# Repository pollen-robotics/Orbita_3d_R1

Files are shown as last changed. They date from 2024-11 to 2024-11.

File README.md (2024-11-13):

# Orbita_3d_R1
All you need to make your own Orbita_3d Joint!

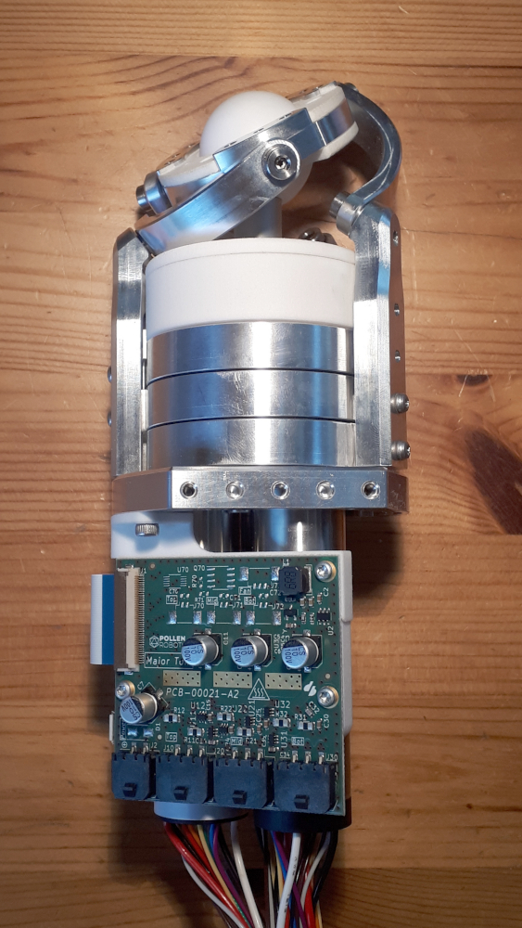
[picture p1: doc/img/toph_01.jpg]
3d view - Major_Tom


## Basically
Please find:
 - Electronic boards that controls (elec_Houston), drives (elec_Major_Tom) and measures (elec_Pacman) the Orbita 3d Joint over 12V-supplied Dynamixel bus.
 - Firmware gather communication (Dynamixel library) and motor control (SimpleFOC library)
 - Cables

## Licences
 - Firmware is under Apache-2.0 licence
 - Electronic/Cables is under CC-BY-SA-NC Licence

## Patents
https://patents.google.com/patent/FR3141363A1

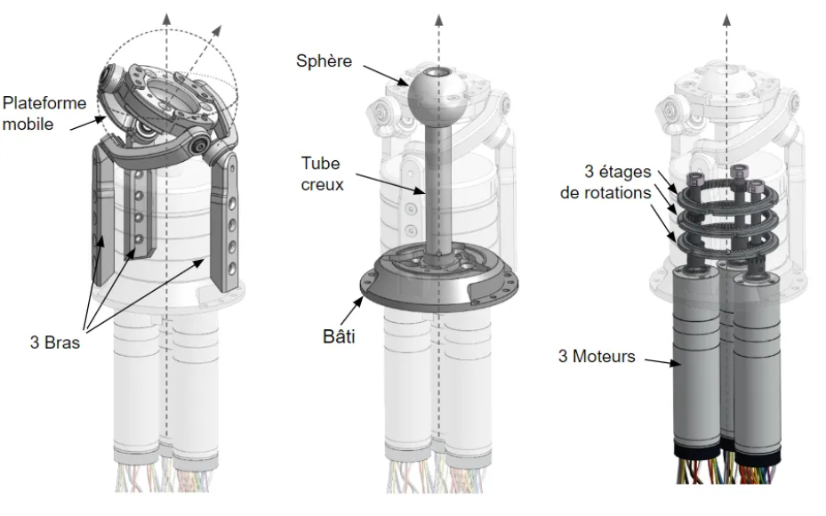
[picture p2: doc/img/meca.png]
3d view - Mecanique - FR


## Contact
contact@pollen-robotics.com

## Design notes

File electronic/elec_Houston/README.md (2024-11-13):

# Houston Electronic Board

Houston board is basically a STM32G4 microcontroller that focuses on driving 3 BLDC motors. It gets 3 Hall effects or encoders on motors and absolute positions behind reduction through SPI encoders.

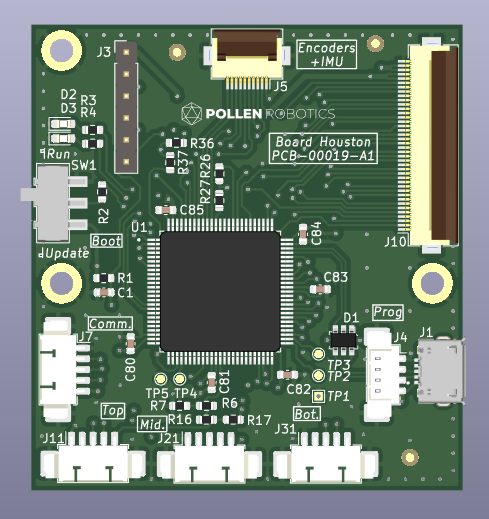
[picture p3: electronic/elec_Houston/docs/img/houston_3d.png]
houston board 3d image


## Basically
 - 50 x 54 mm
 - Powered in 3V3 through the large flat flexible connector J10
 - 5V should also be provided since it supplies encoders J11/21/31
 - Designed with KiCAD 6.0

## ST configuration

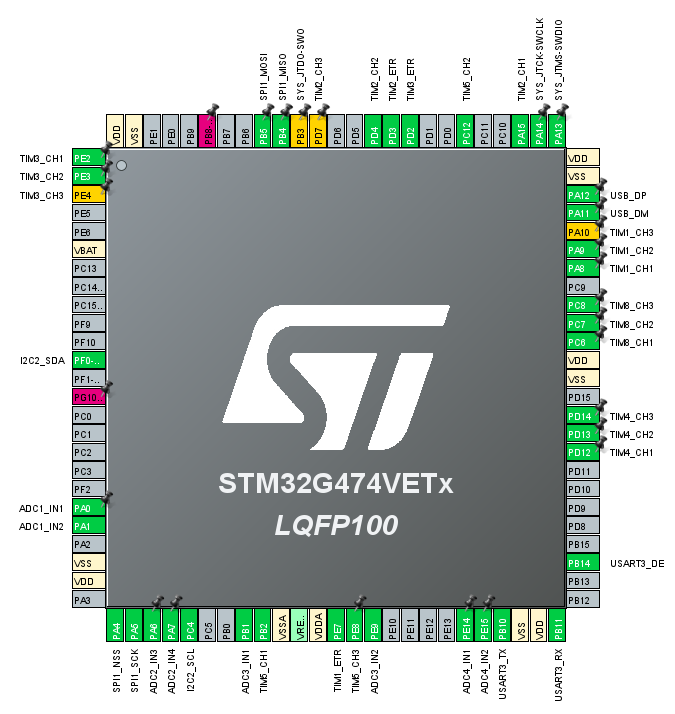
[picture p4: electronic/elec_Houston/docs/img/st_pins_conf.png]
houston board 3d image


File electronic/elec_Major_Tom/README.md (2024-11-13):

# Major Tom Electronic Board

Major Tom is a power board driving 3 BLDC motors. It also add 3 temperature measurements and a fan control.

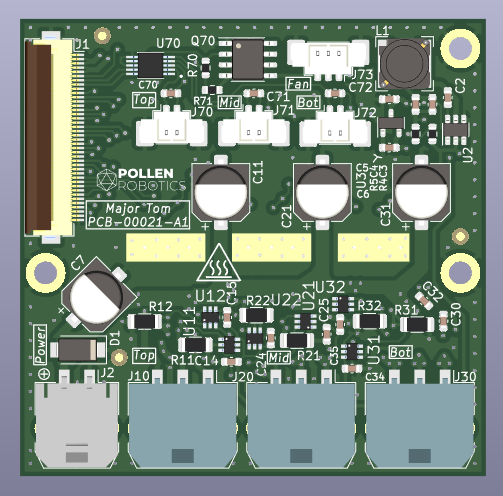
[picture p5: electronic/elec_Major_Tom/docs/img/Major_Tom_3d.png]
Major Tom board 3d image


## Basically
 - 55 x 54 mm
 - Powered in 12V or in 24V.
 - Drive 3 BLDC motors with DRV8313 (2,5 A peak)
 - Designed with KiCAD 6.

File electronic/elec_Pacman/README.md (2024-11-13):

# Pacman Electronic Board

Pacman board gathers 3 absolute encoders with an IMU. It is set at the top of the Orbita system and sends angular positions of the 3 axis + IMU data. It is connected to the Houston board through a FFC.

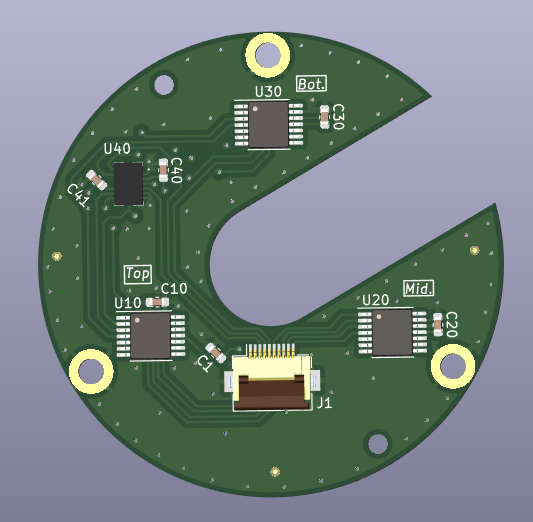
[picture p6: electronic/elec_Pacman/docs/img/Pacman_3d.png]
Pacman board 3d image


## Basically
 - 49 mm diameter with a 13 mm slot
 - Powered in 3V3
 - Common SPI, differents CS pins.

## Notas
 - all components are on the bottom side since the encoders are facing down the motors.

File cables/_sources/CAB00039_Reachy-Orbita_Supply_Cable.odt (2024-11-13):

CAB-00039 – Supply Cable – Orbita

Ver. | Date | Pub | Chk | Description
A1 | 12/01/2023 | EB | AC | Initial drawing.
B1 | 14/02/2023 | EB | AC | Turned into a Y cable to supply Reachy’s antennas.

1. Purpose

This cable supplies Orbita Motors Drivers (ASE00038 Major Tom) from Reachy’s Power Supply Board. The small part (Y cable) supply Reachy’s head through Orbita. This cable is made for Reachy 1.2.

2. Bill of Material

Item | Description | L (mm) | Qtty | Ref. Farnell / RS
Wire | 0,3 mm² | 200 | 2
Hirose DF11 Fem. Housing 8 ways | DF11-8DS-2C | | 1 | 1688304 /
MicroFit Fem. Housing 2 ways | 43645-0200 | | 1 | 3076015 /
MicroFit Male Housing 2 ways | 43640-0201 | | 1 | 3076118 /
Contacts for DF11 | DF11-2428SC | | 2 | 1688393 /
Contacts for MicroFit | 43031-0001 | | 2 | 1653819 /
Contacts for MicroFit | 46235-0001 | | 2 | 2284551 /
Prolongateur | 22 AWG – 16 AWG | | 4 | 587321 /

3. Assembly

Molex Microfit Contacts are crimped with Molex 64016-0201 Tool.

Hirose DF11 Contacts are crimped with Hirose HT801/DF11-2428S(A) Tool

4. Drawing

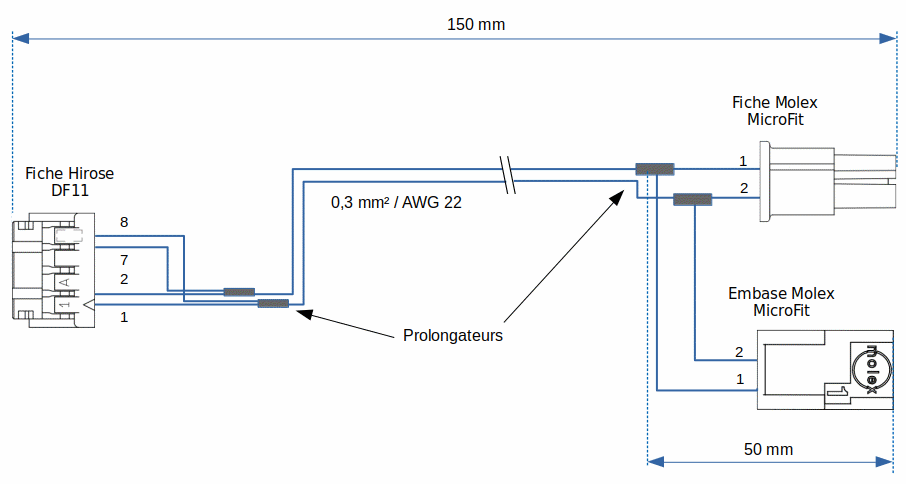
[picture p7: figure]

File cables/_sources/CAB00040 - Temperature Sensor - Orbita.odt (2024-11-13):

CAB-00040 Temperature Sensor - Orbita

Ver. | Date | Pub | Chk | Description
A1 | 13/01/2023 | EB | AC | Initial drawing.

1. Purpose

This temperature sensor is actually a bipolar transistor, its base on the linear relationship between base-emitter voltage and temperature changes. Temperatures are read by the MAX31730 on Major Tom Board.

2. Bill of Materials

Item | Description | L (mm) | Qtté | Ref. Farnell / RS
Wire | 0,15 mm² | ?? | 2
Molex PicoBlade Fem. Housing 2 ways | 51021-0200 | | 1 | /
Contacts for PicoBlade | 50079-8000 | | 2 | /
2N3904 | Transistor TO-92 | | 1 | 1574370 /
Gaine thermo | | 10 | 2

3. Assembly

Molex PicoBlade Contacts are crimped with Tool Molex 63811-0000.

4. Drawing

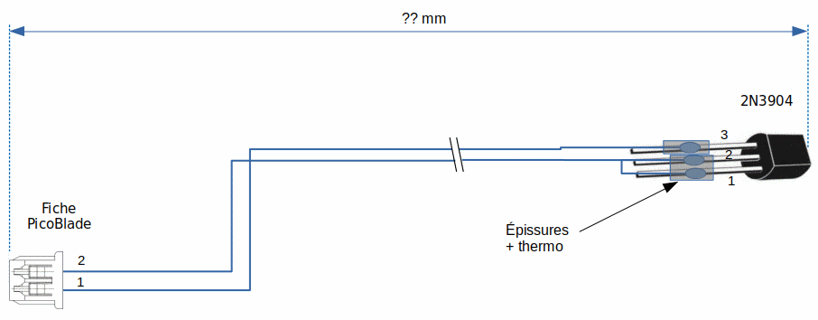
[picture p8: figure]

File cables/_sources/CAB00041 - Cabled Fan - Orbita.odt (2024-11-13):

CAB-00041 – Cabled Fan - Orbita

Ver. | Date | Pub | Chk | Description
A1 | 16/01/2023 | EB | AC | Initial drawing.

1. Purpose

This temperature sensor is actually a bipolar transistor, its base on the linear relationship between base-emitter voltage and temperature changes. Temperatures are read by the MAX31730 on Major Tom Board.

2. Bill of Materials

Item | Description | L (mm) | Qtté | Ref. Farnell / RS
Fan - 12V | RS Pro 668-8808 | | 1 | / 668-8808
Molex PicoBlade Fem. Housing 3 ways | 51021-0300 | | 1 | /
Contacts for PicoBlade | 50079-8000 | | 2 | /

3. Assembly

Molex PicoBlade Contacts are crimped with Tool Molex 63811-0000.

4. Drawing

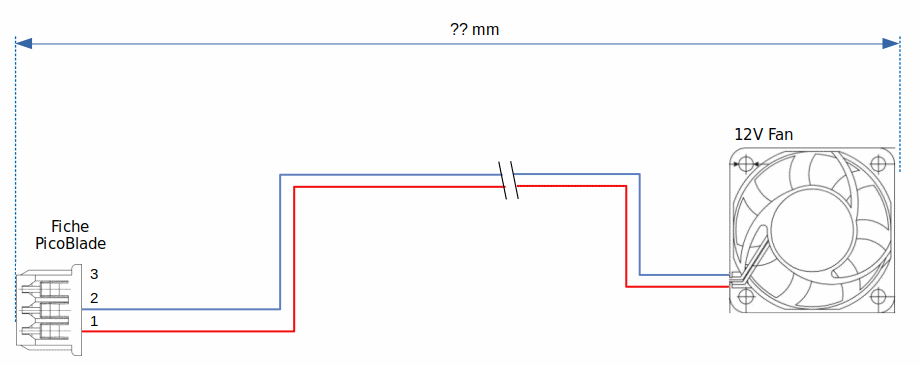
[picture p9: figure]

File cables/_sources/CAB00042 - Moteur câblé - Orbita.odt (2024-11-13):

CAB-00042 – Wired Motor – Orbita

Ver. | Date | Pub | Chk | Description
A1 | 24/01/2023 | EB | AC | Initial drawing.
B1 | 27/03/2023 | EB | AC | Now using Hall sensors

1. Description

24V BLDC Motor (+Reduction + Encoder) wired for Orbita.

2. Bill of Material

Item | Description | L (mm) | Qtté | Ref. Farnell / RS
BLDC Motor 24V + Reductor + Encoder | ECXTQ22M+GPX22R1C+ENX22 | | 1 | Provided par Pollen
Molex PicoBlade Fem. Housing 5 ways | 51021-0500 | | 1 | /
Contacts for PicoBlade | 50079-8000 | | 5 | /
Molex MicroFit Fem. Housing 3 ways | 43645-0300 | | 1 | /
Contacts for MicroFit | 46235-0001 | | 3 | 2284551 /
Gaine thermo

3. Assembly

Molex PicoBlade Contacts are crimped with the Molex 63811-0000 Tool.

Molex MicroFit Contacts are crimped with the Molex 64016-0201 Tool.

4. Drawing

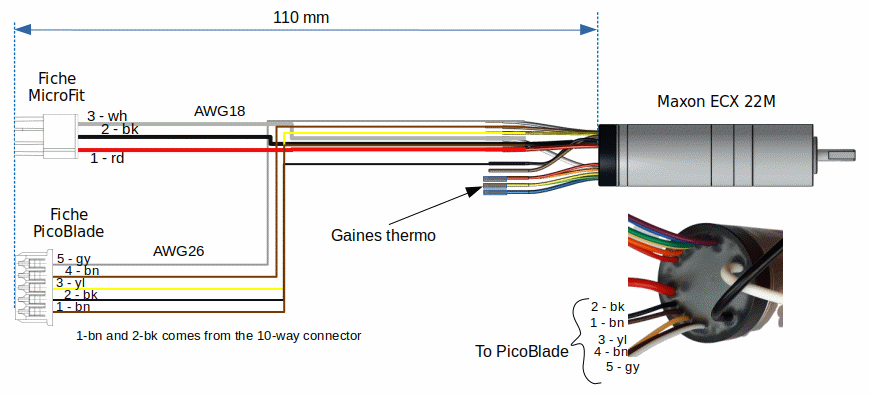
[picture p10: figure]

5. Nota

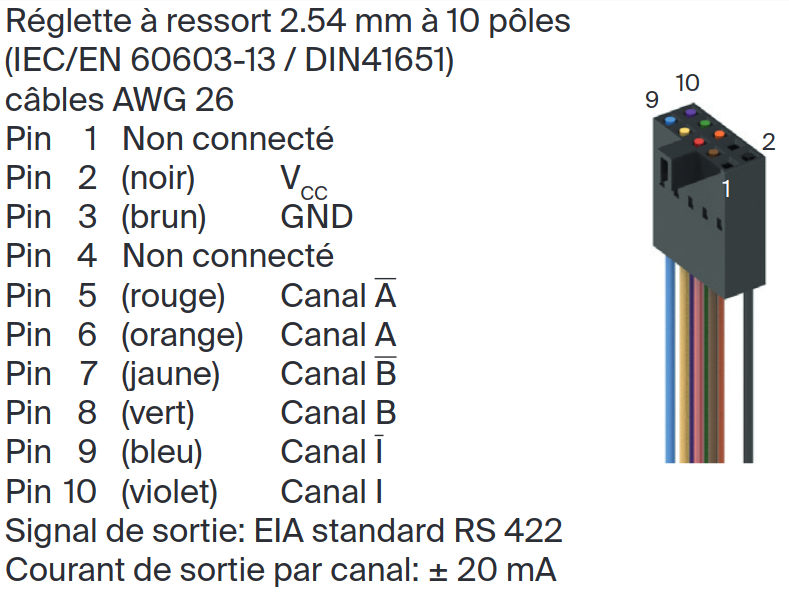
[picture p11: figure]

Please note that the wires 1-brown and 2-black must be taken from the 10-way connector pin #2 and #3.

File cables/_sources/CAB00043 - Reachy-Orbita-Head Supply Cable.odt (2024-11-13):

CAB-00043 – Reachy-Orbita-Head-Supply Cable

Ver. | Date | Pub | Chk | Description
A1 | 14/02/2023 | EB | AC | Initial drawing.

1. Description

Delivering 12V from PCB Major Tom to DXL-Fan-Luos Module in order to supply the antenna’s motors. Please note that this cable goes through Orbita and thus requires to be made directly on Orbita.

2. Bill of Material

Item | Description | L (mm) | Qtté | Ref. Farnell / RS
Wire | 0,3 mm² | 350 | 2
Hirose DF11 Fem. Housing 8 ways | DF11-8DS-2C | | 1 | 1688304 /
MicroFit Fem. Housing 2 ways | 43645-0200 | | 1 | 3076015 /
Contacts for DF11 | DF11-2428SC | | 2 | 1688393 /
Contacts for MicroFit | 46235-0001 | | 2 | 2284551 /
Prolongateur | 22AWG - 16AWG | | 2 | 587321 /

3. Assembly

Hirose DF11 Contacts are crimped with Hirose HT801/DF11-2428S(A) Tool

Molex MicroFit Contacts are crimped with the Molex 64016-0201 Tool.

4. Drawing

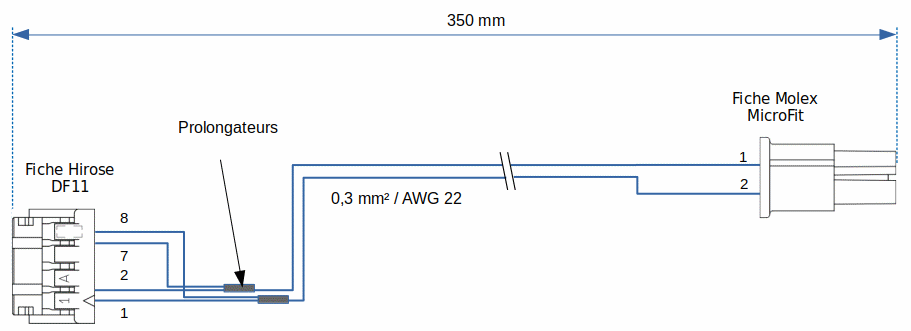
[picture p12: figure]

5. Nota

Again, note that this cable requires to be made directly on Orbita.

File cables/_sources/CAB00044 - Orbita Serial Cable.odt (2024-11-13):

CAB-00044 – Orbita Serial Cable

Ver. | Date | Pub | Chk | Description
A1 | 10/03/2023 | EB | SN | Initial drawing.
B1 | 14/04/2023 | EB | AC | Extra length added after prototyping.

1. Description

FTDI-232-3V3 cable that allows communication with Houston/Orbita.

2. Bill of Material

Item | Description | L (mm) | Qtté | Ref. Farnell / RS
USB-Serial converter | TTL-234X-3V3 | 250 | 1 | 2753009 /
Molex PicoBlade Fem. Housing 5 ways | 51021-0500 | | 1 | /
Contacts for PicoBlade | 50079-8000 | | 3 | /
Gaine thermo | | | | /

3. Assembly

Molex PicoBlade Contacts are crimped with Tool Molex 63811-0000.

4. Drawing

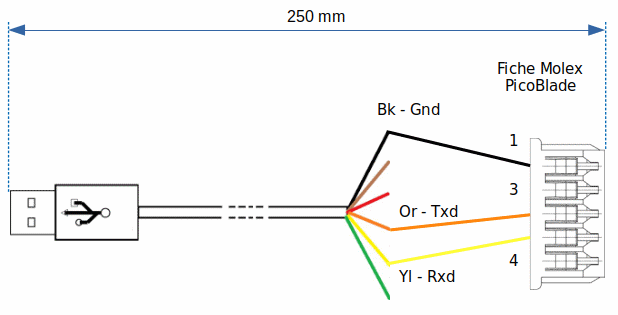
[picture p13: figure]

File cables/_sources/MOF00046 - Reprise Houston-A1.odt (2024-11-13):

MOF-00046 – Reprise Houston-A1

Ver. | Date | Pub | Chk | Description
A1 | 13/03/2023 | EB | SN | Initial drawing.

1. Description

Réorientation des signaux des Hall/encoders et des sorties d’erreurs des drivers de manière à répartir ces signaux sur des broches interruptibles, 5V-tolerant et possédant des EXTI distincts.

2. Modifications

## Passer en mode Hall Sensors

Changer les résistances 0R pour mettre la carte Houston en mode effets Hall.

- Virer R16 et installer R17
- Virer R26 et installer R27
- Virer R36 et R37.

## Motor Bottom Hall C

Relier le pad supérieur de R37 à la broche 15 du micro :

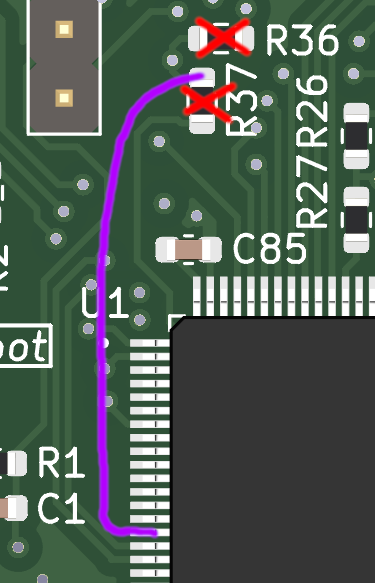
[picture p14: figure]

## Motor Bottom Hall

Couper la piste qui part de J31-3 :

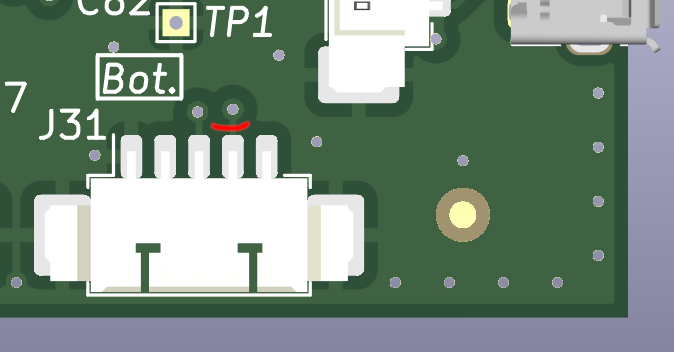
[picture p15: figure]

Relier la broche J31-3 à la broche 5 du micro :

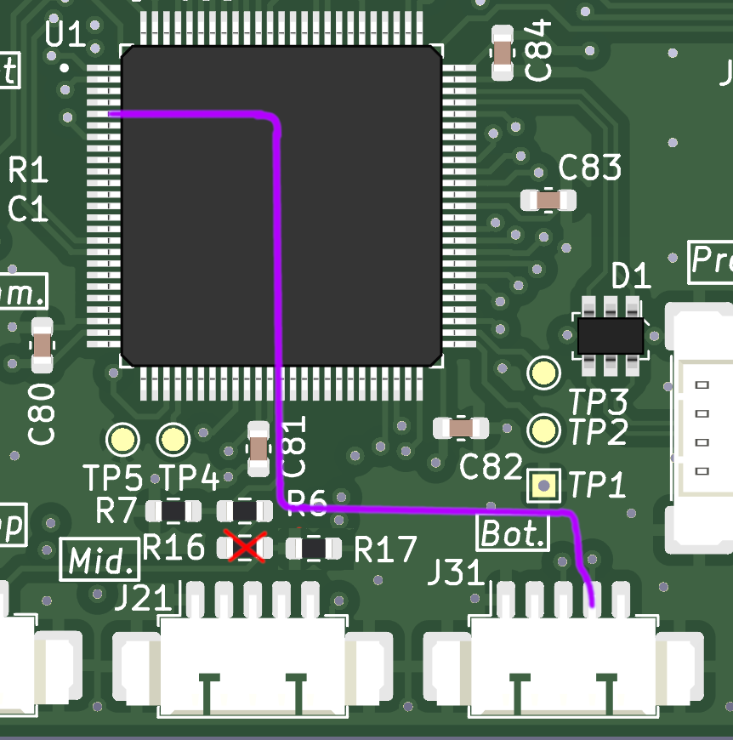
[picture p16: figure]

## Contrôle final :

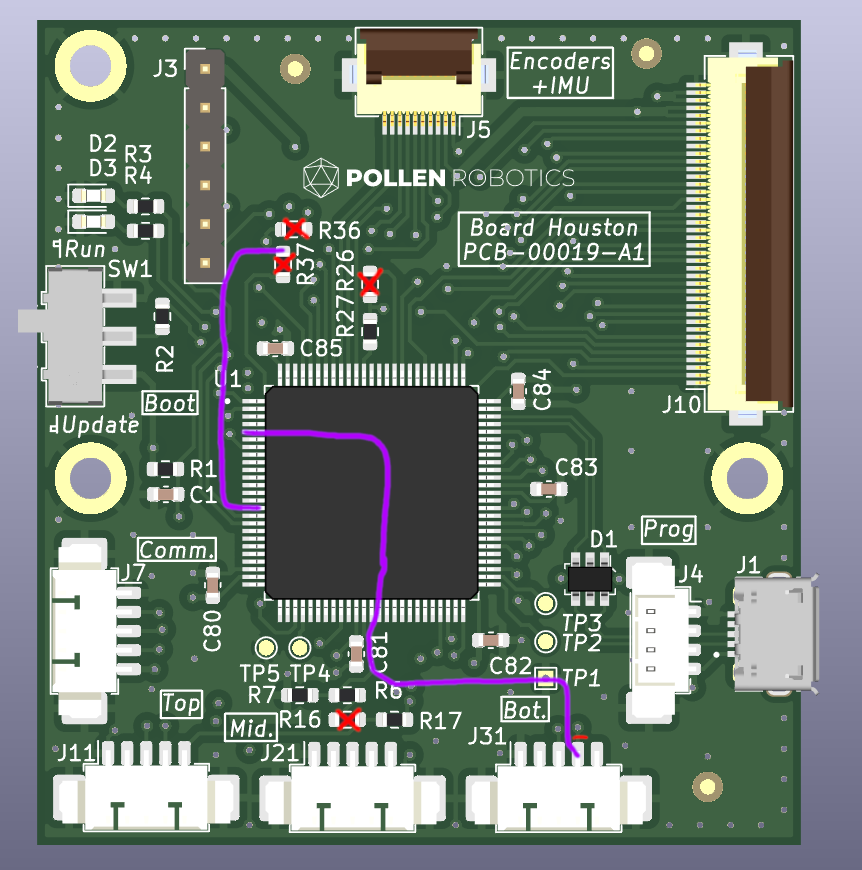
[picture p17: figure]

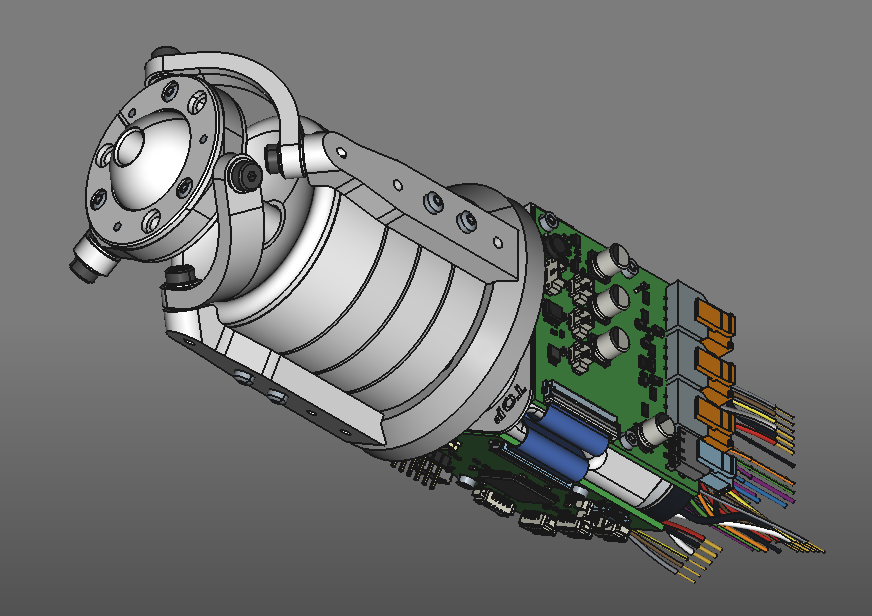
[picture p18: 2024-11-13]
mechanic/Mécanique/Orbita-3D_R1.png

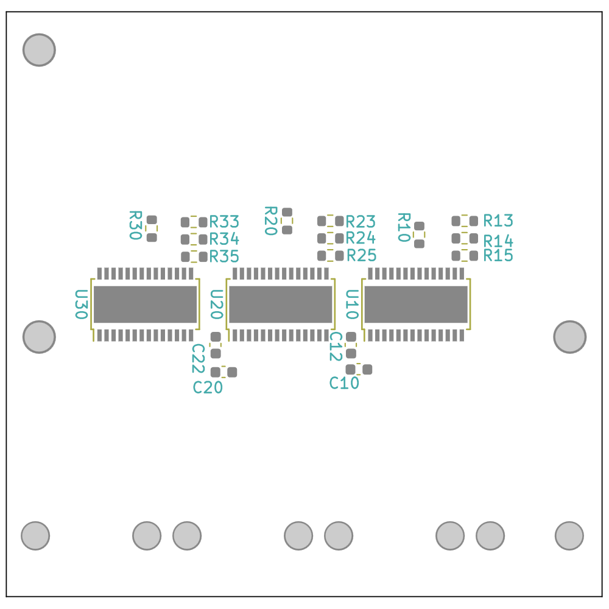
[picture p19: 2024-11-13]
electronic/elec_Major_Tom/fab/ASE00038-A2_Major_Tom_back_ASY.png

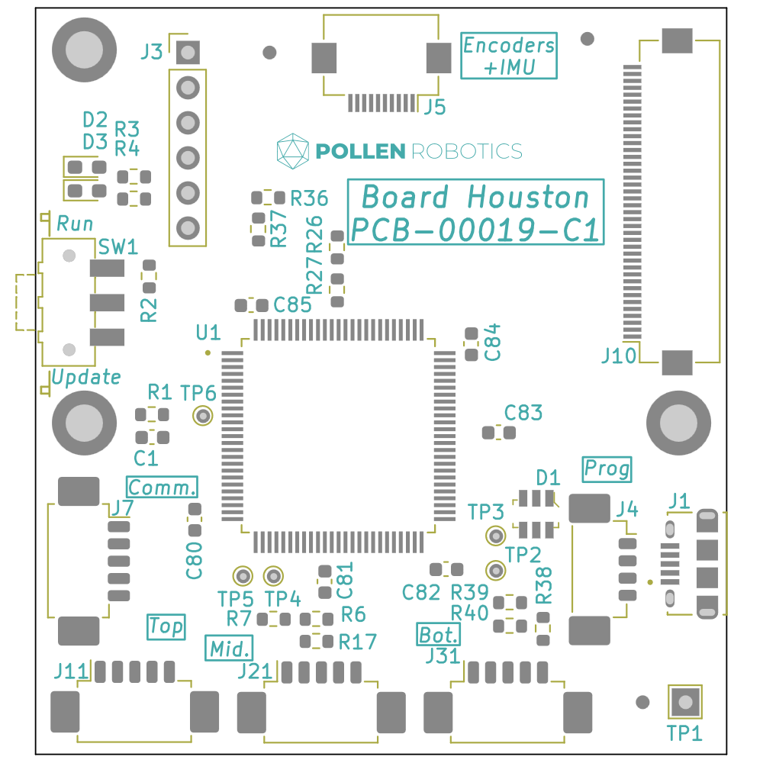
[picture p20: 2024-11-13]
electronic/elec_Houston/fab/ASE00037-C1_carte_Houston_ASY.png

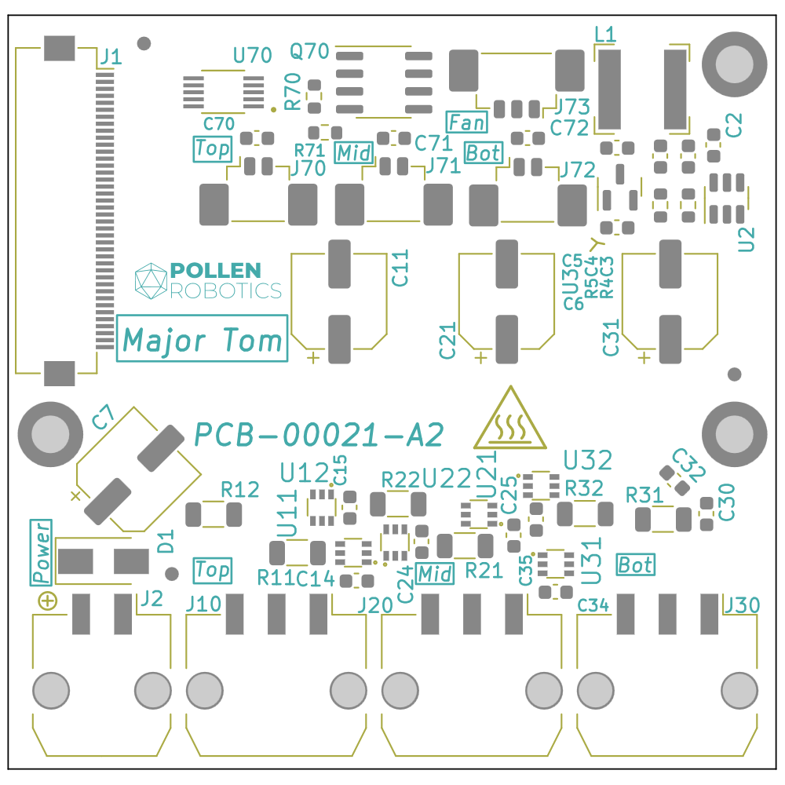
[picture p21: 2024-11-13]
electronic/elec_Major_Tom/fab/ASE00038-A2_Major_Tom_front_ASY.png

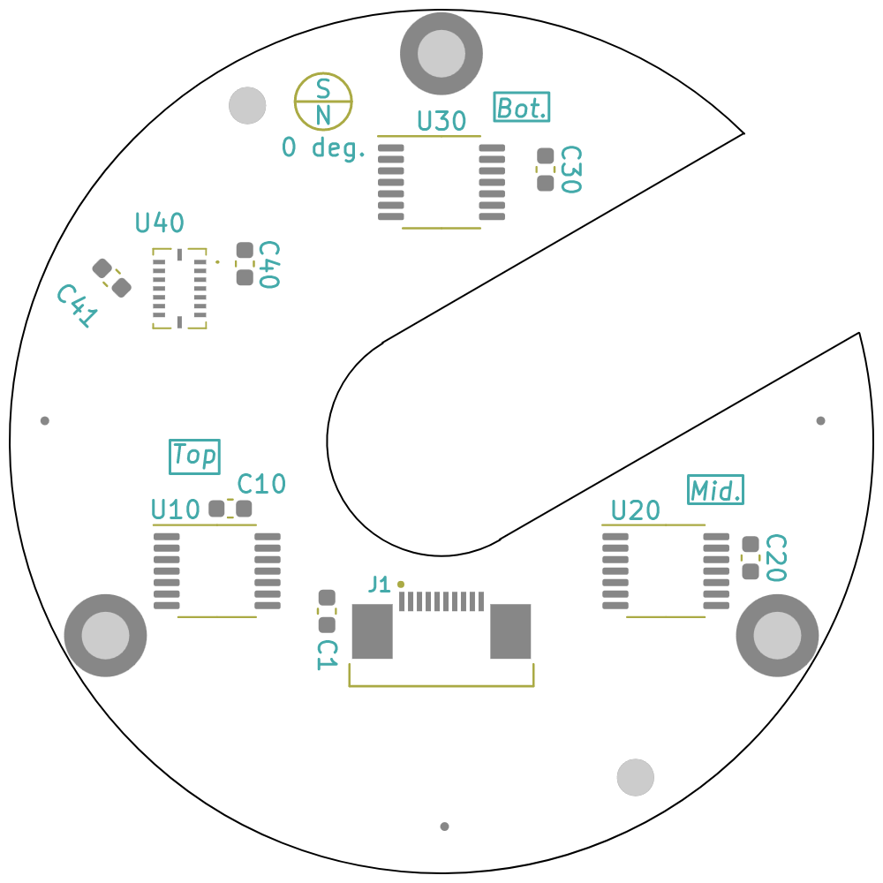
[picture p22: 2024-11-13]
electronic/elec_Pacman/fab/ASE00036-B1_elec_Pacman_ASY.png

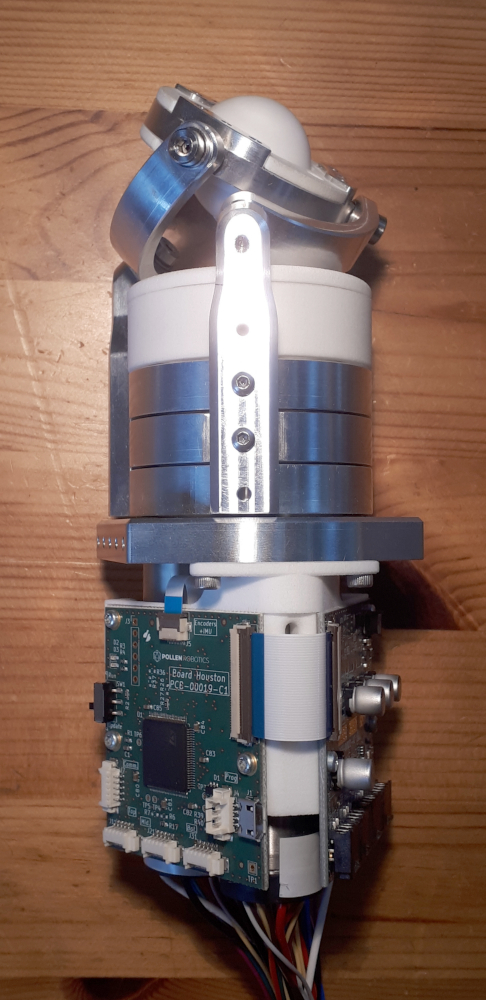
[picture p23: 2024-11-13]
doc/img/toph_02.jpg

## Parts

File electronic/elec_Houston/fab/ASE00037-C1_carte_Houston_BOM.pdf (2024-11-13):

ASE00037 | C1 | Houston | 14/04/2023
Ref. | Value | Description | Qtty | Man. | Man. Ref.
| 100n 6V3 | Capa 0603 | 7 | TDK | CGA3E2X7R1H104K0 80AA
D1 | USBLC6-2SC6 | ESD Protection | 1 | STMicro | USBLC6-2SC6
D2 | Green | Green LED 0603 | 1 | Wurth | 150060VS75000
D3 | Red | Red LED 0603 | 1 | Wurth | 150060RS75000
H5 | PCB00019 | PCB | 1
J1 | 10118194-0001LF | USB Prog Connector | 1 | Amphenol FCI | 10118194-0001LF
J3 | DNP - SIL6 | SWDebug Connector | 1 | Harwin | M20-9990646
J4 | Pico4 | Fake USB Connector | 1 | Molex | 53398-0471
J5 | FFC 0,5 mm 10w | Encoders/IMU Connector | 1 | Hirose | FH12-10S-0.5SH(55)
J7, J11, J21, J31 | Pico5 | Comm. Connector | 4 | Molex | 53261-0571
J10 | FFC 0,5 mm 40w | Microcontroller Connector | 1 | Hirose | FH12-40S-0.5SH(55)
R1 | 100k | Res. 0603 | 1 | Yageo | RC0603FR-07100KL
R2 | 10k | Res. 0603 | 1 | Yageo | RC0603FR-0710KL
R3, R4 | 470R | Res. 0603 | 2 | Yageo | RC0603FR-07470RL
R6 | DNP-4k7 | Res. 0603 | 1
R7 | DNP-9k1 | Res. 0603 | 1
0R | Res. 0603 | 4 | Yageo | RC0603FR-070RL
DNP-0R | Res. 0603 | 4
SW1 | SW_SPDT | Boot switch | 1 | C&K Switches | JS102011SAQN
U1 | STM32G474 | Microcontroller | 1 | STMicro | STM32G474VET6

C1, C80, C81,
C82, C83, C84,
C85

R17, R27, R38,
R39
R26, R36, R37,
R40

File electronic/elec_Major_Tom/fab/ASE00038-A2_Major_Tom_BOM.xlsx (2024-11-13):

ASE00038 | A2 | Major Tom | 2023-01-09
Ref. | Value | Description | Qtty | Man. | Man. Ref.
C2, C10, C14, C15, C20, C24, C25, C30, C34, C35 | 100n 63V | Capa 0603 | 10 | TDK | CGA3E2X7R1H104K080AA
C3, C4 | 22u 6V3 | Capa 0603 | 2 | Murata | GRM188R61A226ME15D
C5, C6 | 1u 6V3 | Capa 0603 | 2 | TDK | C1608X7R1A105K080AC
C7, C11, C21, C31 | 10u 63V | Capa diam. 6,3 / pas 7,7 | 4 | Multicomp | MCESL100V106M6.3X7.7
C12, C22, C32 | 10n 63V | Capa 0603 | 3 | TDK | CGA3E2C0G1H103J080AA
C70, C71, C72 | DNP-100p | Capa 0603 | 3
D1 | DNP-D_TVS_uni | Diode TVS unidir. 12V | 1 | STMicro | SMAJ12A
J1 | FFC 0,5 mm 40w | Microcontroller Connector | 1 | Hirose | FH12-40S-0.5SH(55)
J2 | MicroFit2 | Power Supply Connector | 1 | Molex | 43650-0210
J10, J20, J30 | MicroFit3 | Motor Phases Connector | 3 | Molex | 43650-0310
J70, J71, J72 | DNP-Pico2 | Temperature Connector | 3 | Molex | 53398-0271
J73 | DNP-Pico3 | Fan Connector | 1 | Molex | 53398-0371
L1 | 6,8u 2A | Inductor 6,8u 2A 6x6 mm | 1 | Bourns | SRN6045TA-6R8M
Q70 | DNP-AUIRF7341Q | DNP-MOSFET Double | 1 | Infineon | AUIRF7341Q
R4 | 180k | Res. 0603 | 1 | Yageo | RC0603FR-07180KL
R5 | 20k | Res. 0603 | 1 | Yageo | RC0603FR-0720KL
R10, R13, R14, R15, R20, R23, R24, R25, R30, R33, R34, R35 | 10k | Res. 0603 | 12 | Yageo | RC0603FR-0710KL
R11, R12, R21, R22, R31, R32 | 10m | Power Res. 10m 1206 0,2W | 6 | Panasonic | ERJ8CWFR010V
R70, R71 | DNP-100k | DNP-Res. 0603 | 2
U2 | AP63205 | DC-DC buck converter -> 5V | 1 | Diodes Inc. | AP63205WU
U3 | MCP1700T | LDO Regulator -> 3V3 | 1 | MicroChip | MCP1700T-3302E/TT
U10, U20, U30 | DRV8313 | BLDC Driver 2,5A peak | 3 | TI | DRV8313PWP
U11, U12, U21, U22, U31, U32 | NCS214 | Current Sense Amplifier x100 | 6 | ON Semi | NCS214RSQT2G
U70 | DNP-MAX31730 | DNP-Temperature + Fan Controller | 1 | Maxim Integrated | MAX31730AUB+

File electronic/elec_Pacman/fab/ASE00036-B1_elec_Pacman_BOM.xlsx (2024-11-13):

ASE00036 | B1 | Pacman | 2023-02-27
Ref. | Value | Description | Qtty | Man. | Man. Ref.
C1, C10, C20, C30, C40, C41 | 100nF 6V3 | Capa 0603 | 6 | TDK | CGA3E2X7R1H104K080AA
J1 | FFC 0,5 mm top contacts | FFC 0,5mm Connector 10 pins top contacts | 1 | AMP - TE | 1-1734839-0
U10, U20, U30 | AS5047D | Absolute Angular Encoder | 3 | AMS | AS5047D
U40 | BMI088 | Inertial Measurement Unit | 1 | Bosch Sensortec | BMI088

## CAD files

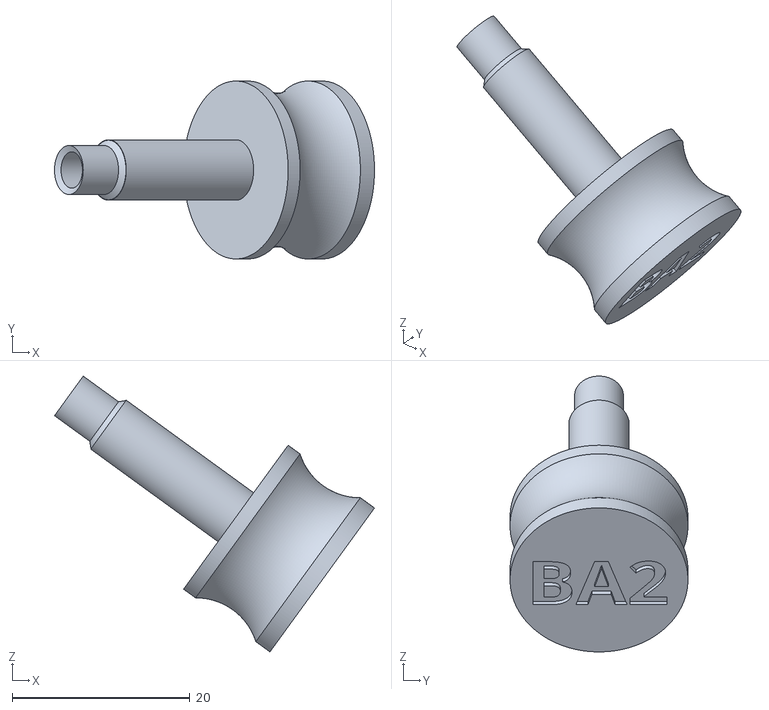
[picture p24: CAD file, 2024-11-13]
mechanic/Assemblage/Outillages/TLG_BA 2.stl
36.0 x 20.0 x 31.0

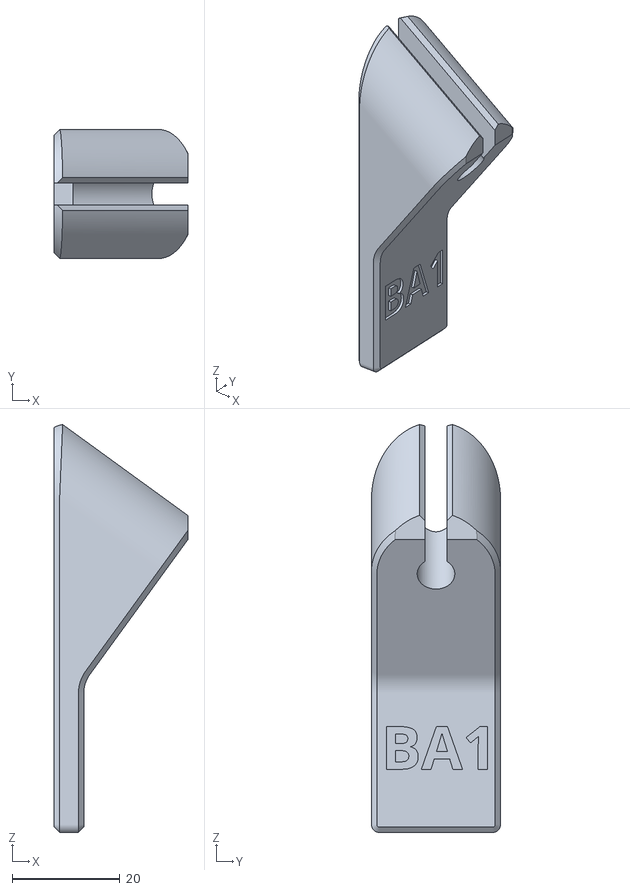
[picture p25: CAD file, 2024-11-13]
mechanic/Assemblage/Outillages/TLG_BA 1.stl
24.8 x 24.0 x 75.9

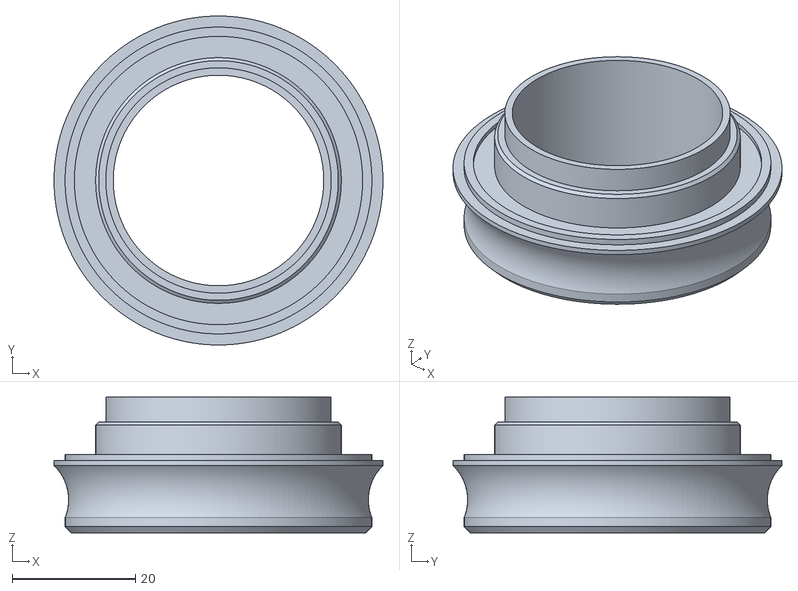
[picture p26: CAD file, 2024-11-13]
mechanic/Assemblage/Outillages/TLG_DC 3.stl
53.3 x 53.3 x 22.0

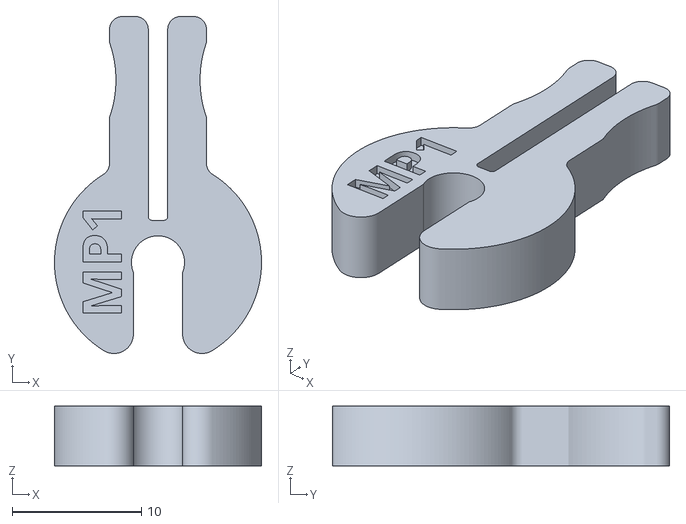
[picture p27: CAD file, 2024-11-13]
mechanic/Assemblage/Outillages/TLG_MP 1.stl
16.0 x 26.0 x 4.60

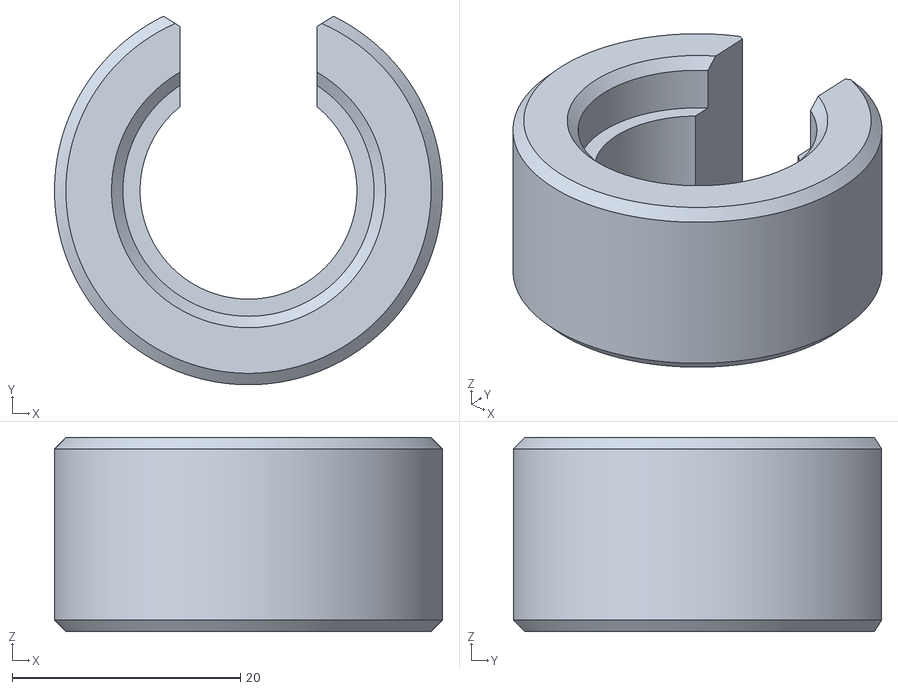
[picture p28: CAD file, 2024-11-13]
mechanic/Assemblage/Outillages/TLG_MP 2.stl
34.0 x 32.3 x 17.0

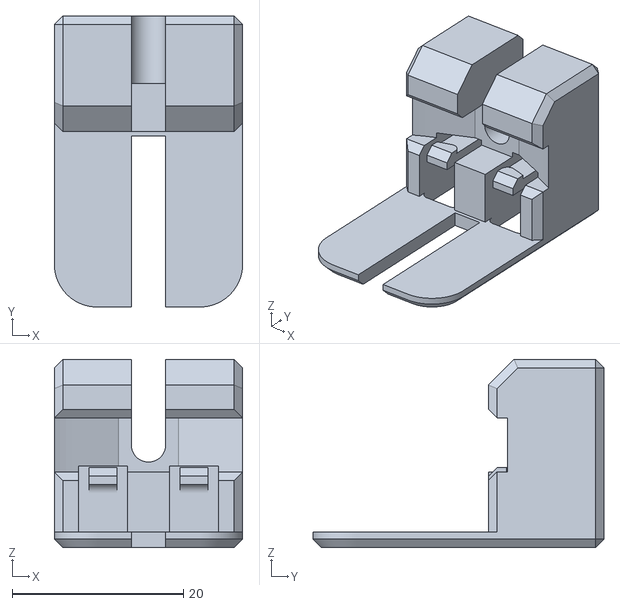
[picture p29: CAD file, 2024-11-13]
mechanic/Assemblage/Outillages/TLG_PA 1.stl
22.0 x 34.0 x 22.0

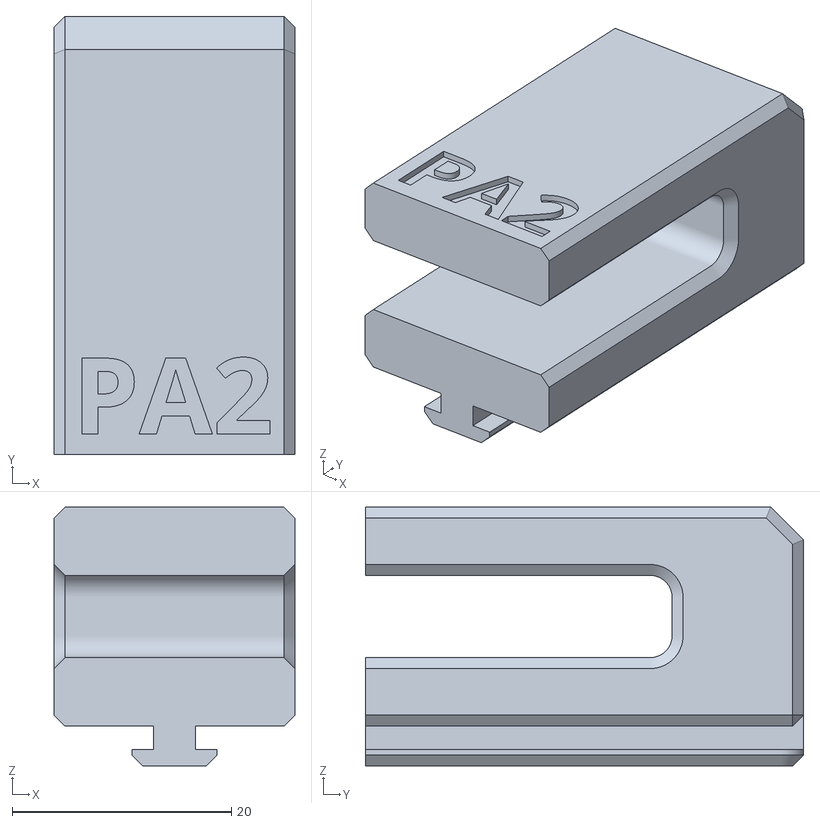
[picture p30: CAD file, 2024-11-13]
mechanic/Assemblage/Outillages/TLG_PA 2.stl
22.0 x 40.0 x 23.6

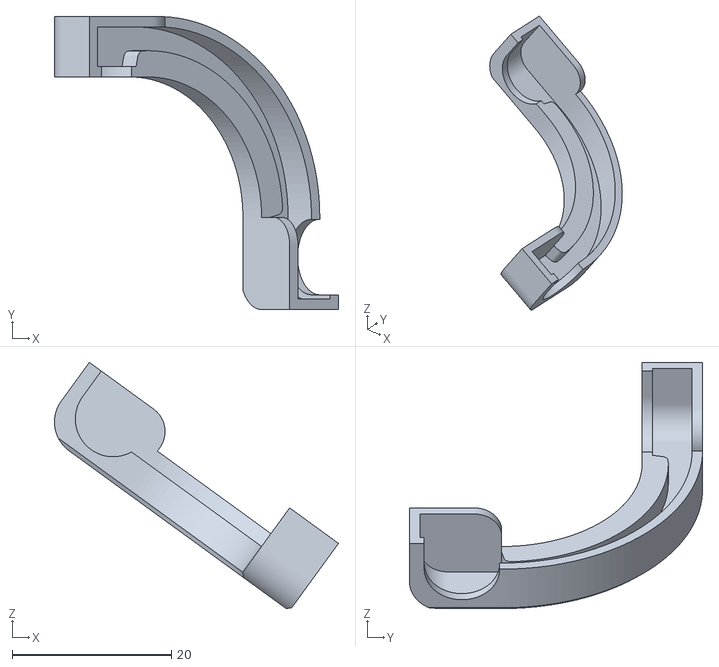
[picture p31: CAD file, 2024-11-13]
mechanic/Assemblage/Outillages/TLG_BP.stl
35.7 x 36.8 x 31.0

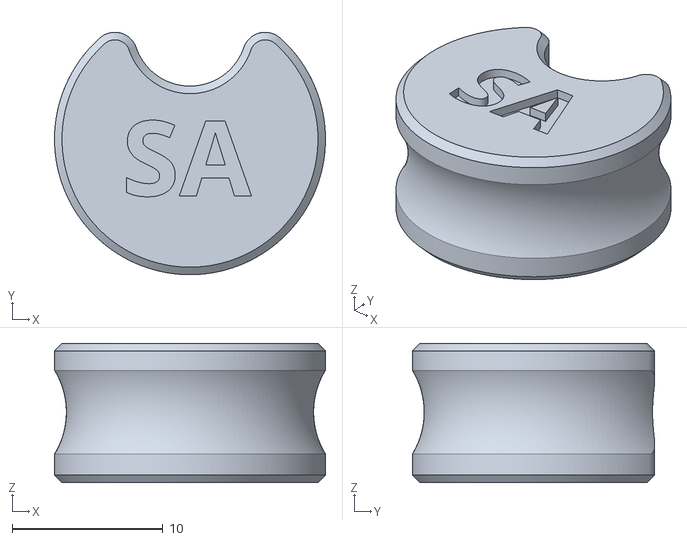
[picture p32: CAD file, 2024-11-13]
mechanic/Assemblage/Outillages/TLG_SA.stl
18.0 x 16.1 x 9.25

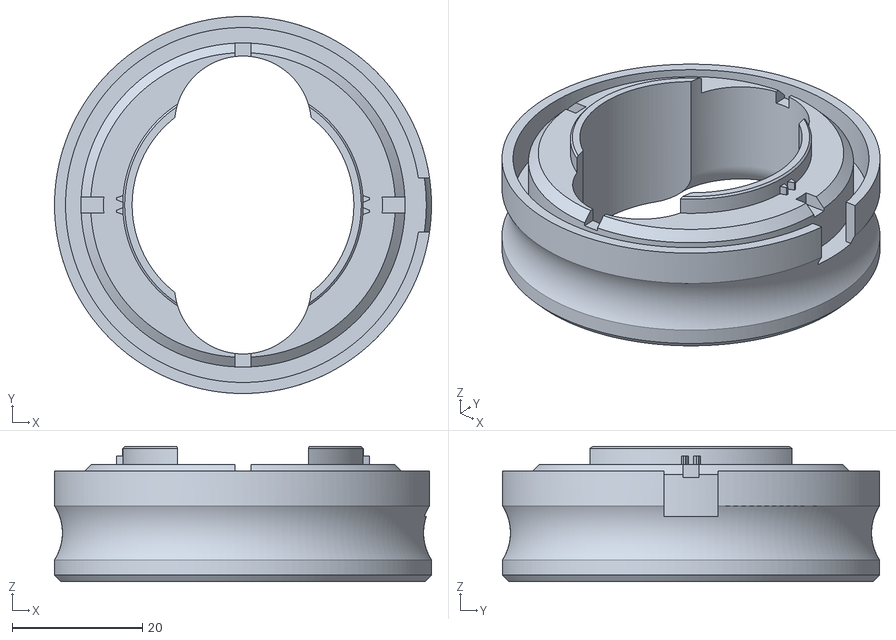
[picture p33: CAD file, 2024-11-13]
mechanic/Assemblage/Outillages/TLG_DC 2.stl
58.0 x 58.0 x 20.8

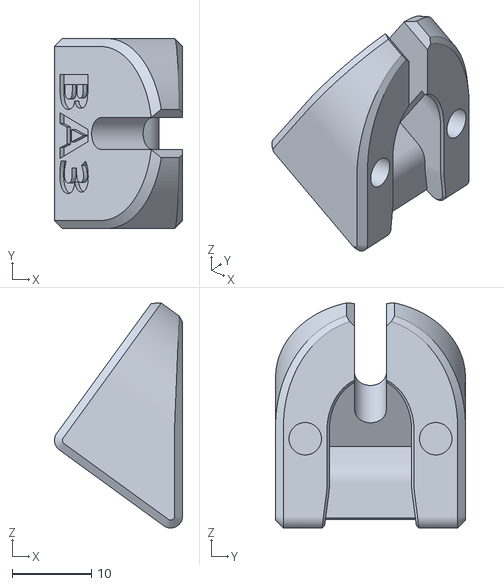
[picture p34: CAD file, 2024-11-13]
mechanic/Assemblage/Outillages/TLG_BA 3.stl
16.2 x 24.0 x 28.4

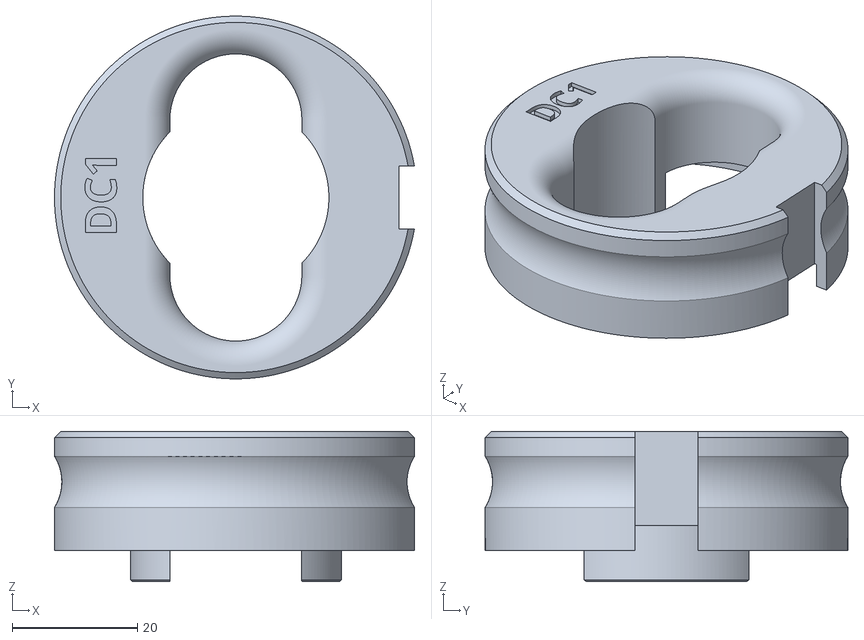
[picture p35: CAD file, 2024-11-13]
mechanic/Assemblage/Outillages/TLG_DC 1.stl
57.5 x 57.9 x 24.0

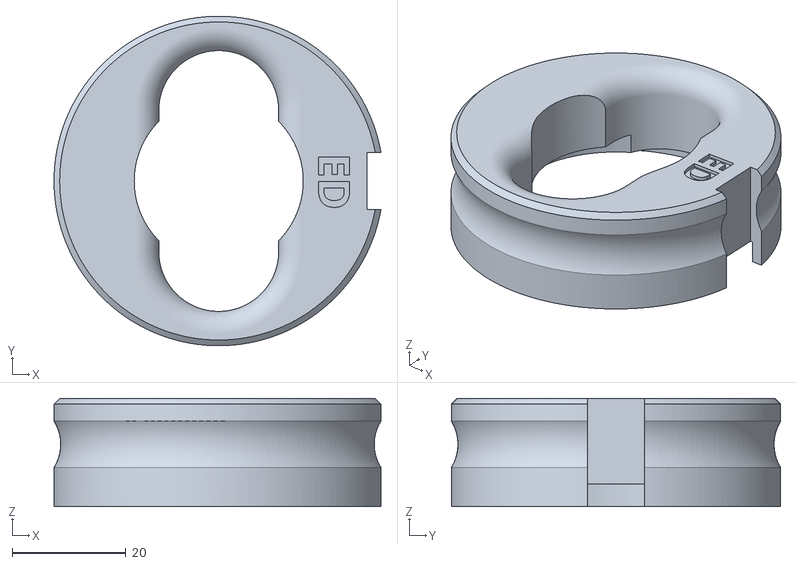
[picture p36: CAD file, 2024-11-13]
mechanic/Assemblage/Outillages/TLG_ED.stl
57.5 x 57.9 x 19.0

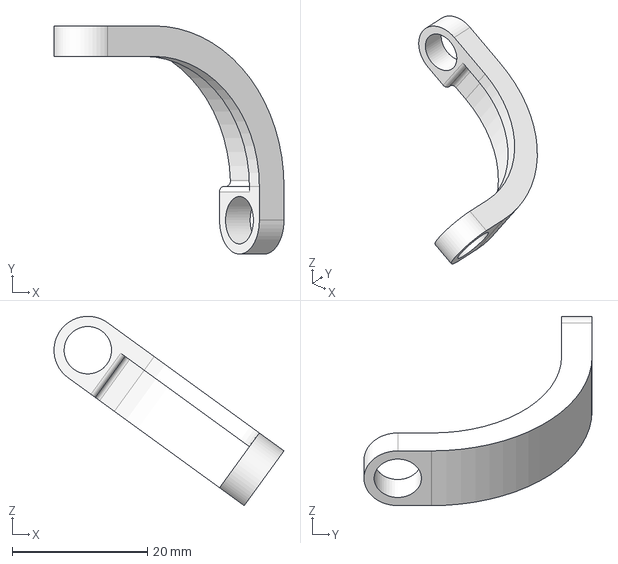
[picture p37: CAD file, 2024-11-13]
mechanic/Mécanique/Orbita metal_B1/MP00006-B1_Moon Arm.step
34.0 x 33.7 x 28.0 mm

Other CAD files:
mechanic/Mécanique/Orbita metal_B1/Settings/Iglidur.3mf
mechanic/Mécanique/Orbita metal_B1/MP00005-B1_Arm.step
mechanic/Mécanique/Orbita metal_B1/PP00014-A1_Ball.stl
mechanic/Mécanique/Orbita metal_B1/PP00016-B1_Plate.stl
mechanic/Mécanique/Orbita metal_B1/MP00001-A2_Basement.step
mechanic/Mécanique/Orbita metal_B1/MP00002-A1_Tube.step
mechanic/Mécanique/Orbita metal_B1/MP00003-A1_Crown.step
mechanic/Mécanique/Orbita metal_B1/MP00004-A1_Crown teeth.step
mechanic/Mécanique/Orbita metal_B1/MP00007-A1_Bottom pinion.step
mechanic/Mécanique/Orbita metal_B1/MP00008-A1_Middle pinion.step
mechanic/Mécanique/Orbita metal_B1/MP00009-A1_Top pinion.step
mechanic/Mécanique/Orbita metal_B1/MP00015-B1_Plate_Ring.step
mechanic/Mécanique/Orbita metal_B1/PP00010-A2_Stage.stl
mechanic/Mécanique/Orbita metal_B1/PP00011-A2_Magnet holder.stl
mechanic/Mécanique/Orbita metal_B1/PP00012-A2_Top.stl
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

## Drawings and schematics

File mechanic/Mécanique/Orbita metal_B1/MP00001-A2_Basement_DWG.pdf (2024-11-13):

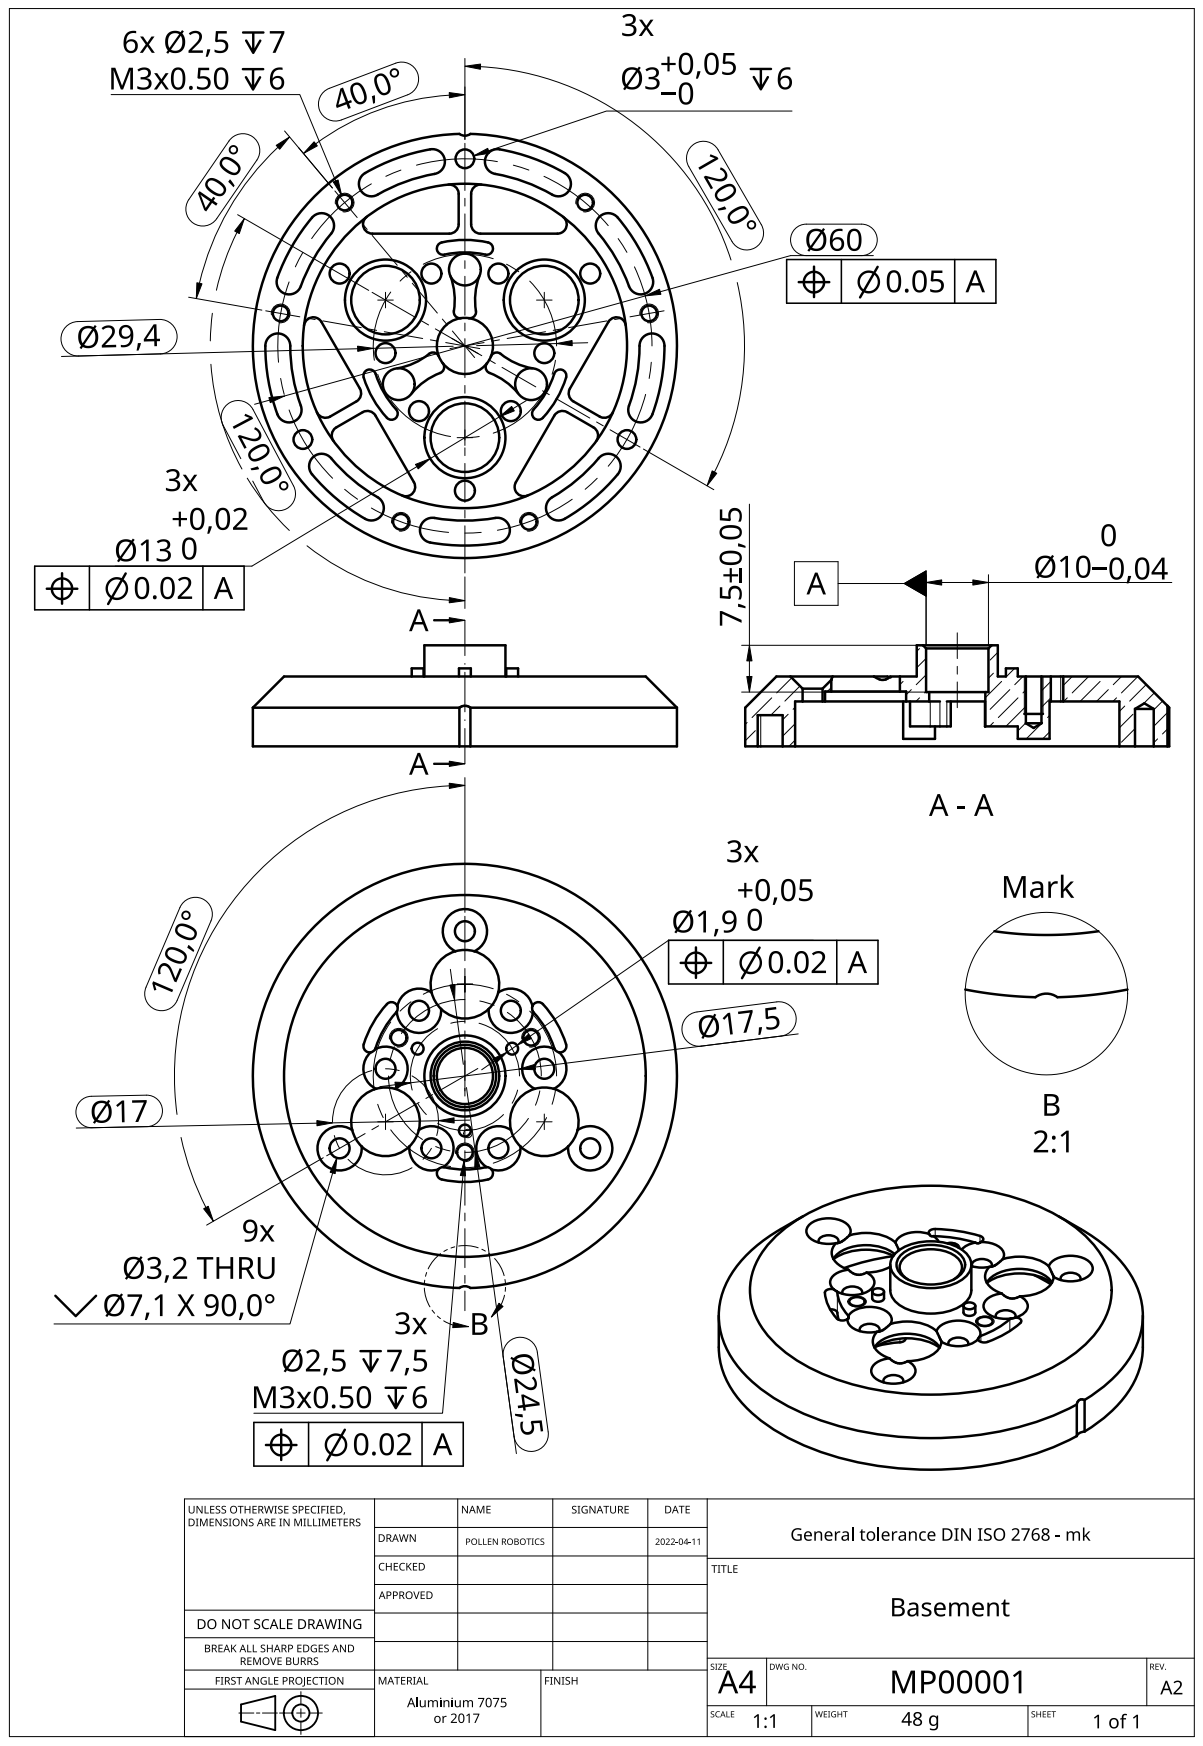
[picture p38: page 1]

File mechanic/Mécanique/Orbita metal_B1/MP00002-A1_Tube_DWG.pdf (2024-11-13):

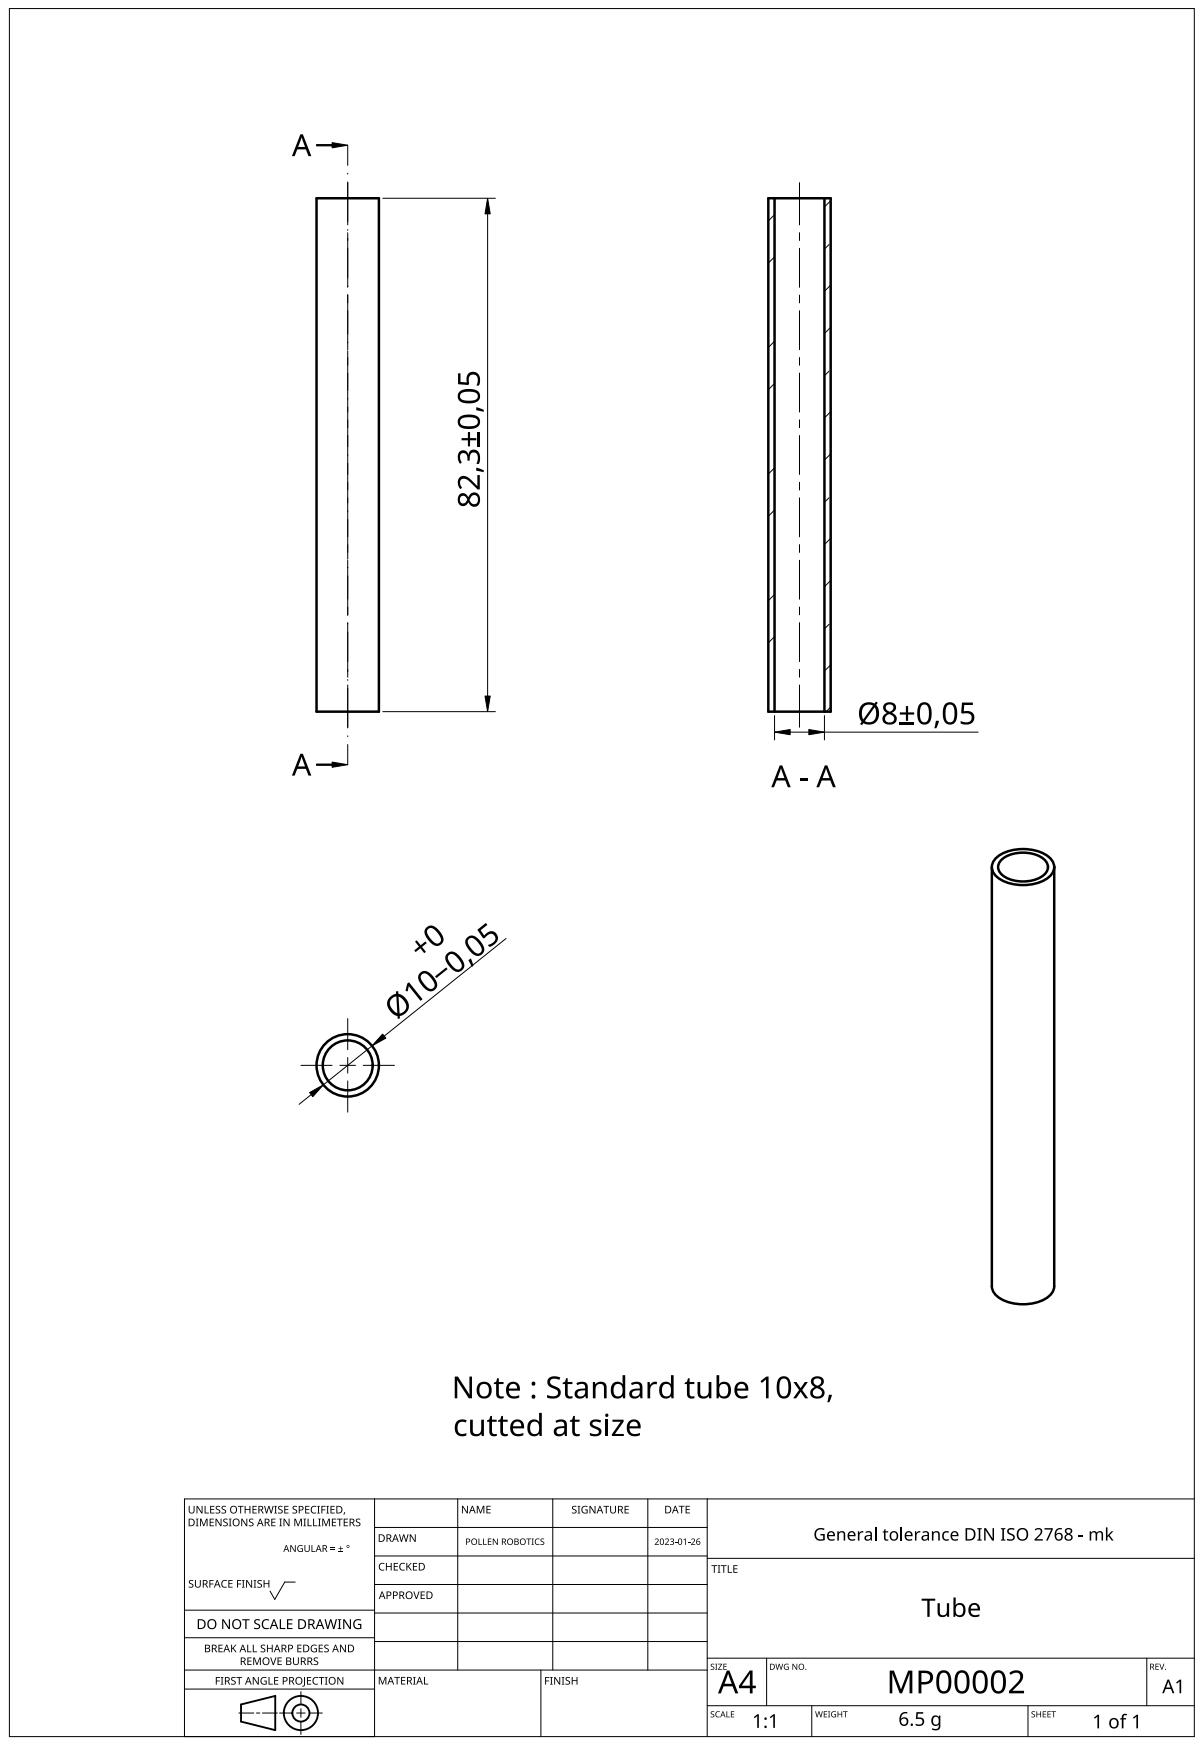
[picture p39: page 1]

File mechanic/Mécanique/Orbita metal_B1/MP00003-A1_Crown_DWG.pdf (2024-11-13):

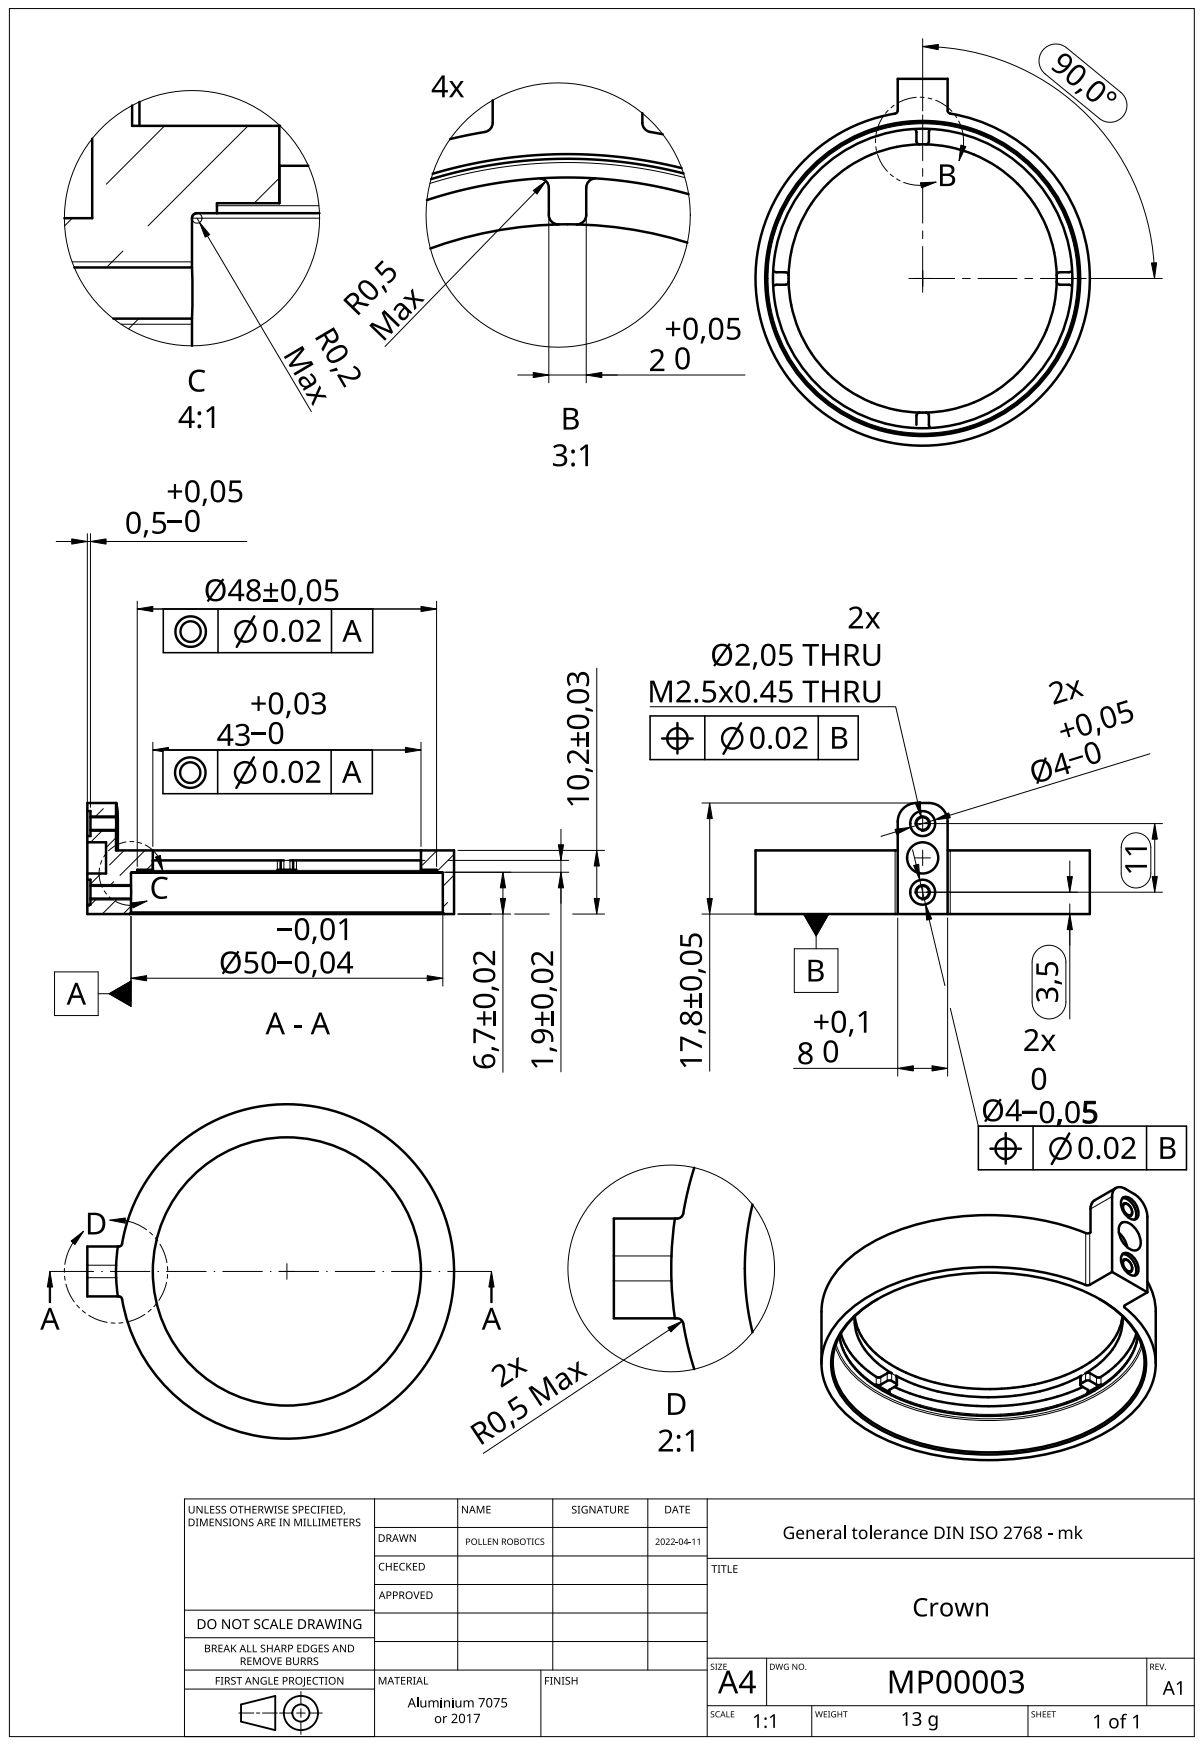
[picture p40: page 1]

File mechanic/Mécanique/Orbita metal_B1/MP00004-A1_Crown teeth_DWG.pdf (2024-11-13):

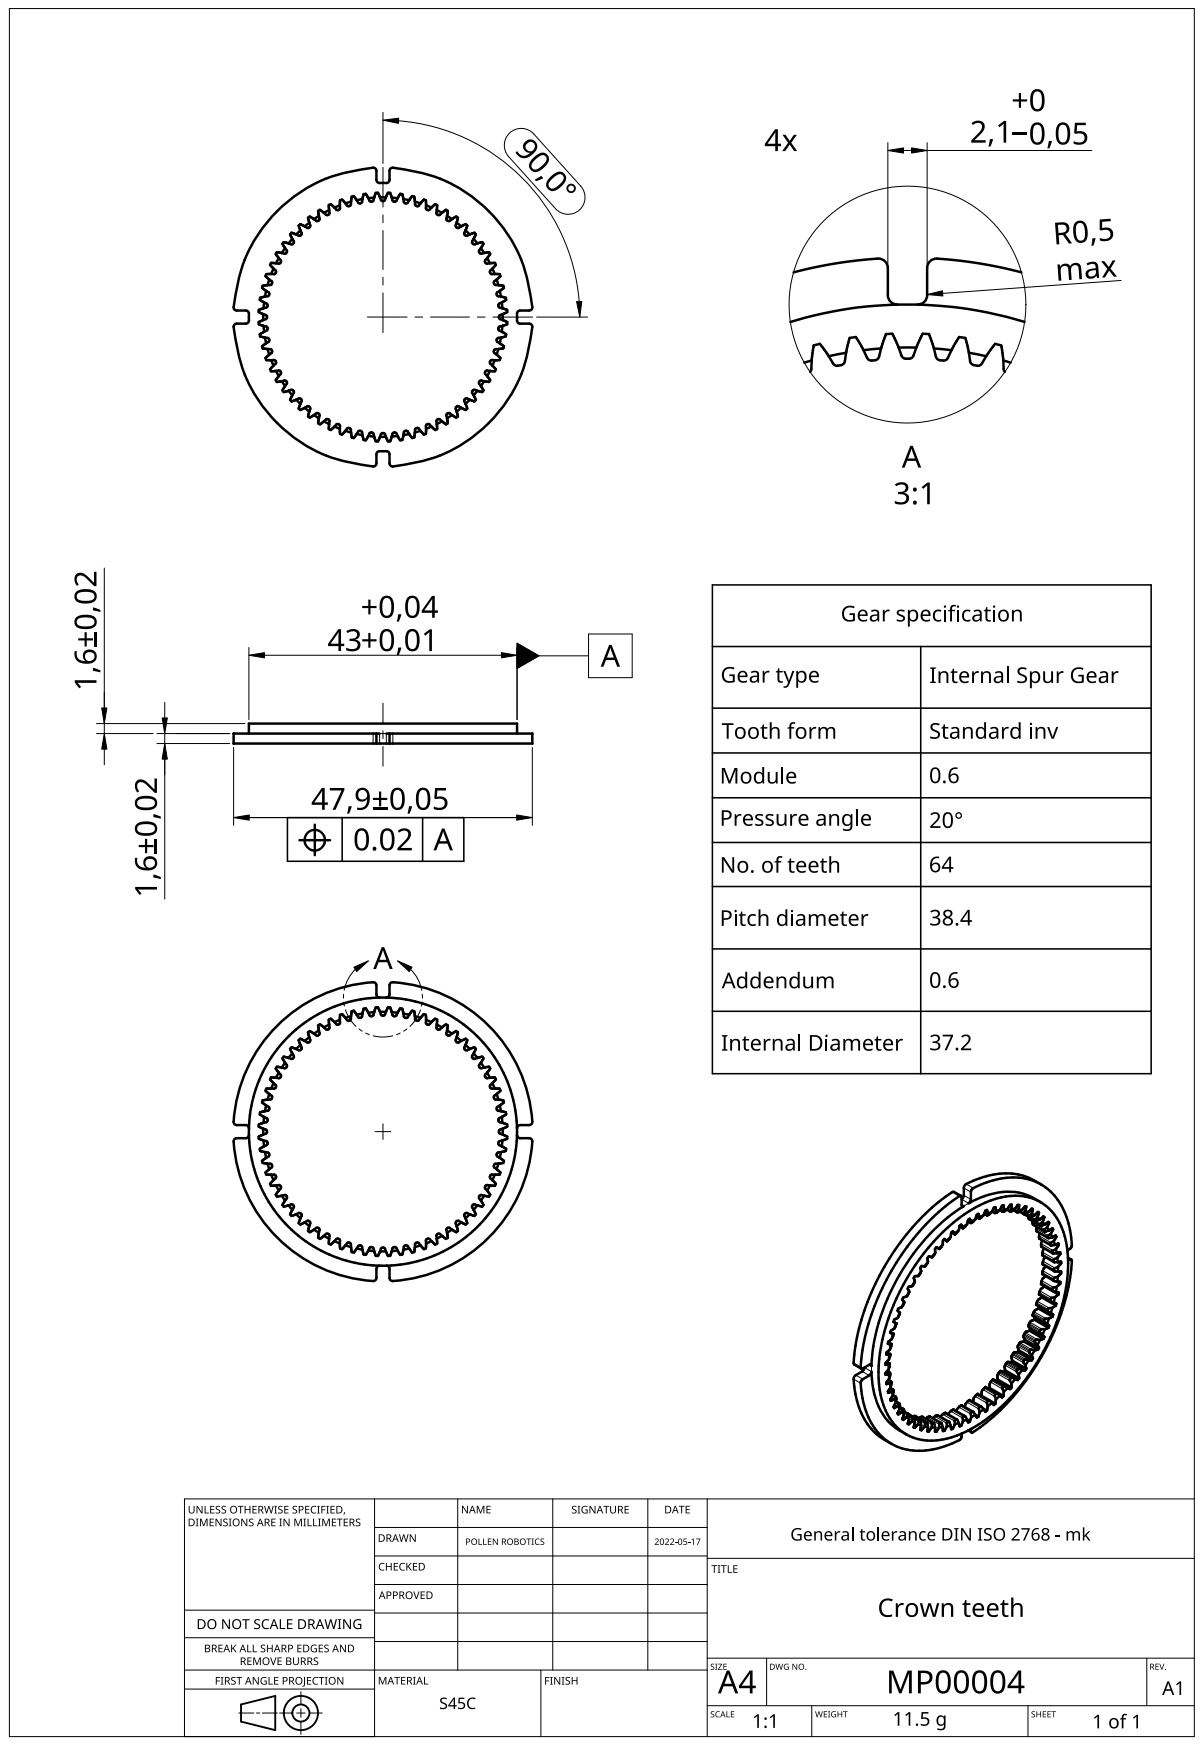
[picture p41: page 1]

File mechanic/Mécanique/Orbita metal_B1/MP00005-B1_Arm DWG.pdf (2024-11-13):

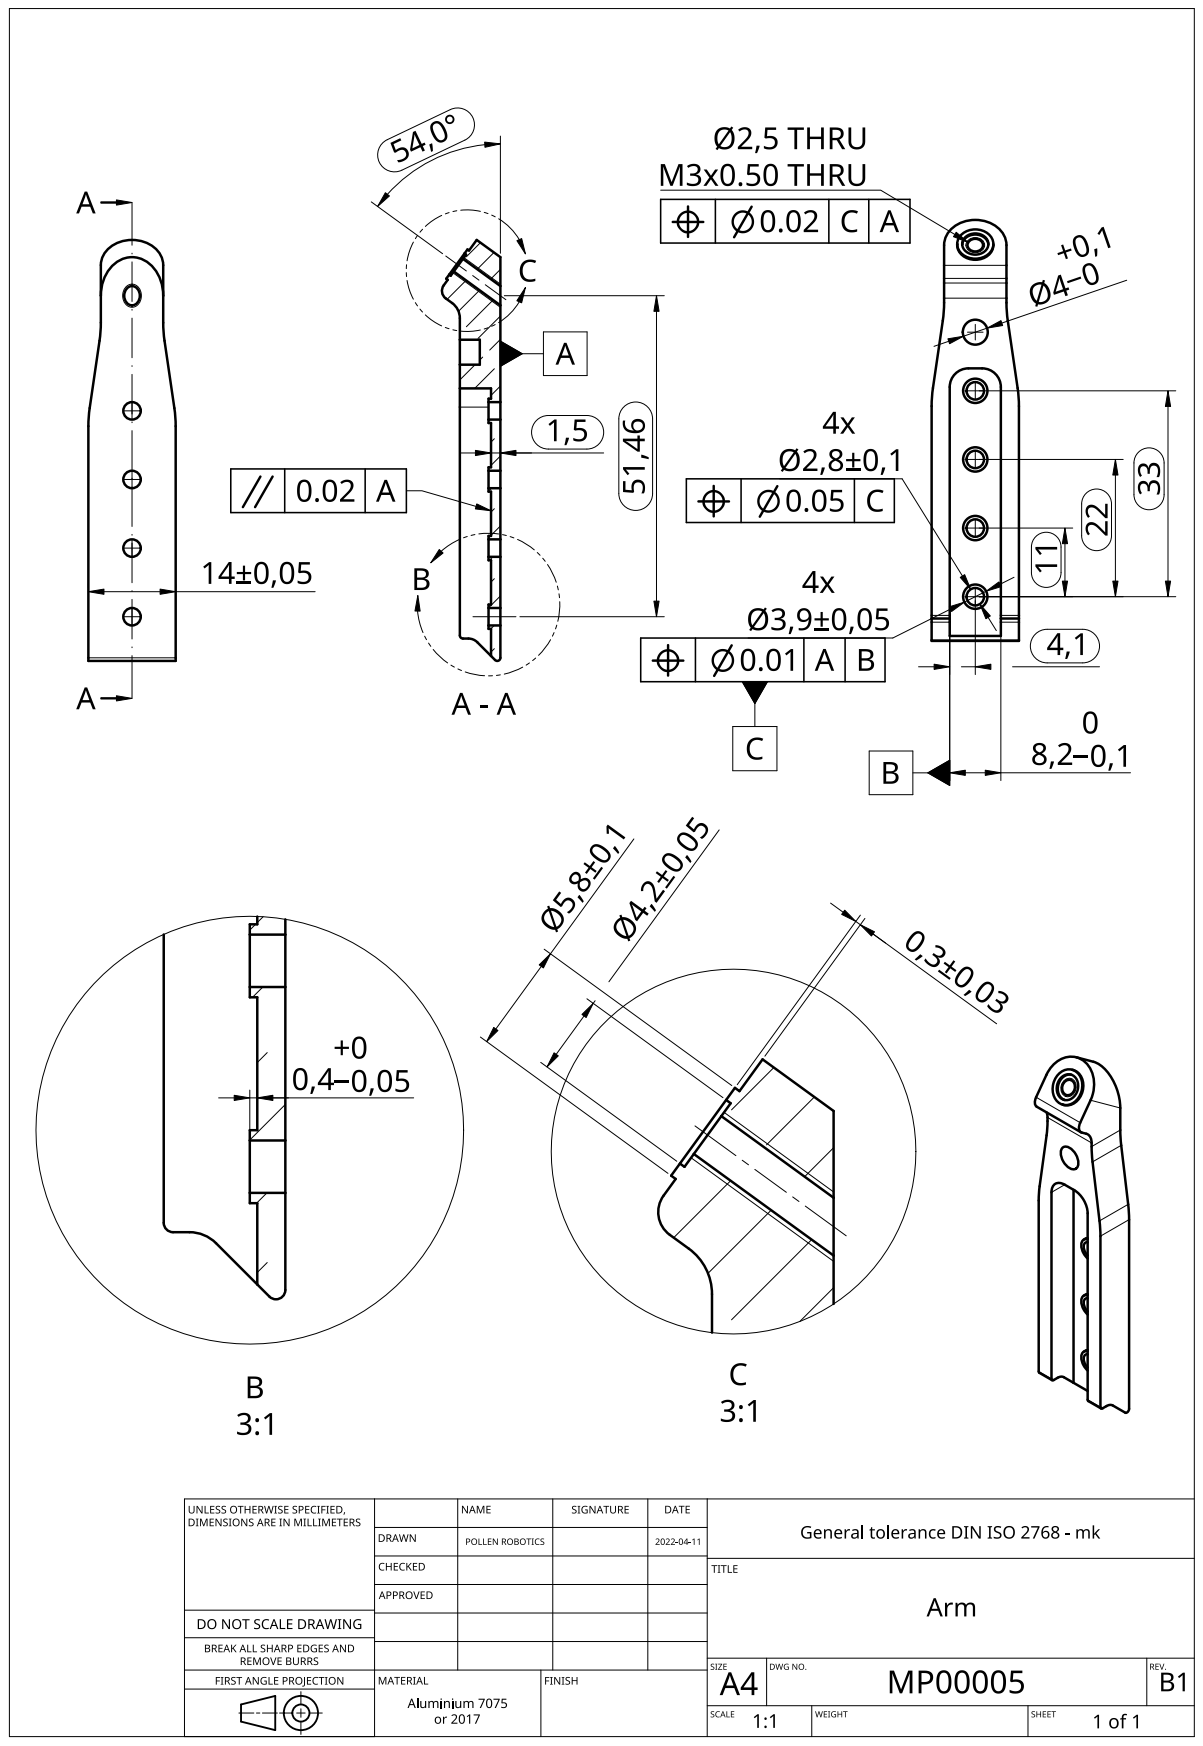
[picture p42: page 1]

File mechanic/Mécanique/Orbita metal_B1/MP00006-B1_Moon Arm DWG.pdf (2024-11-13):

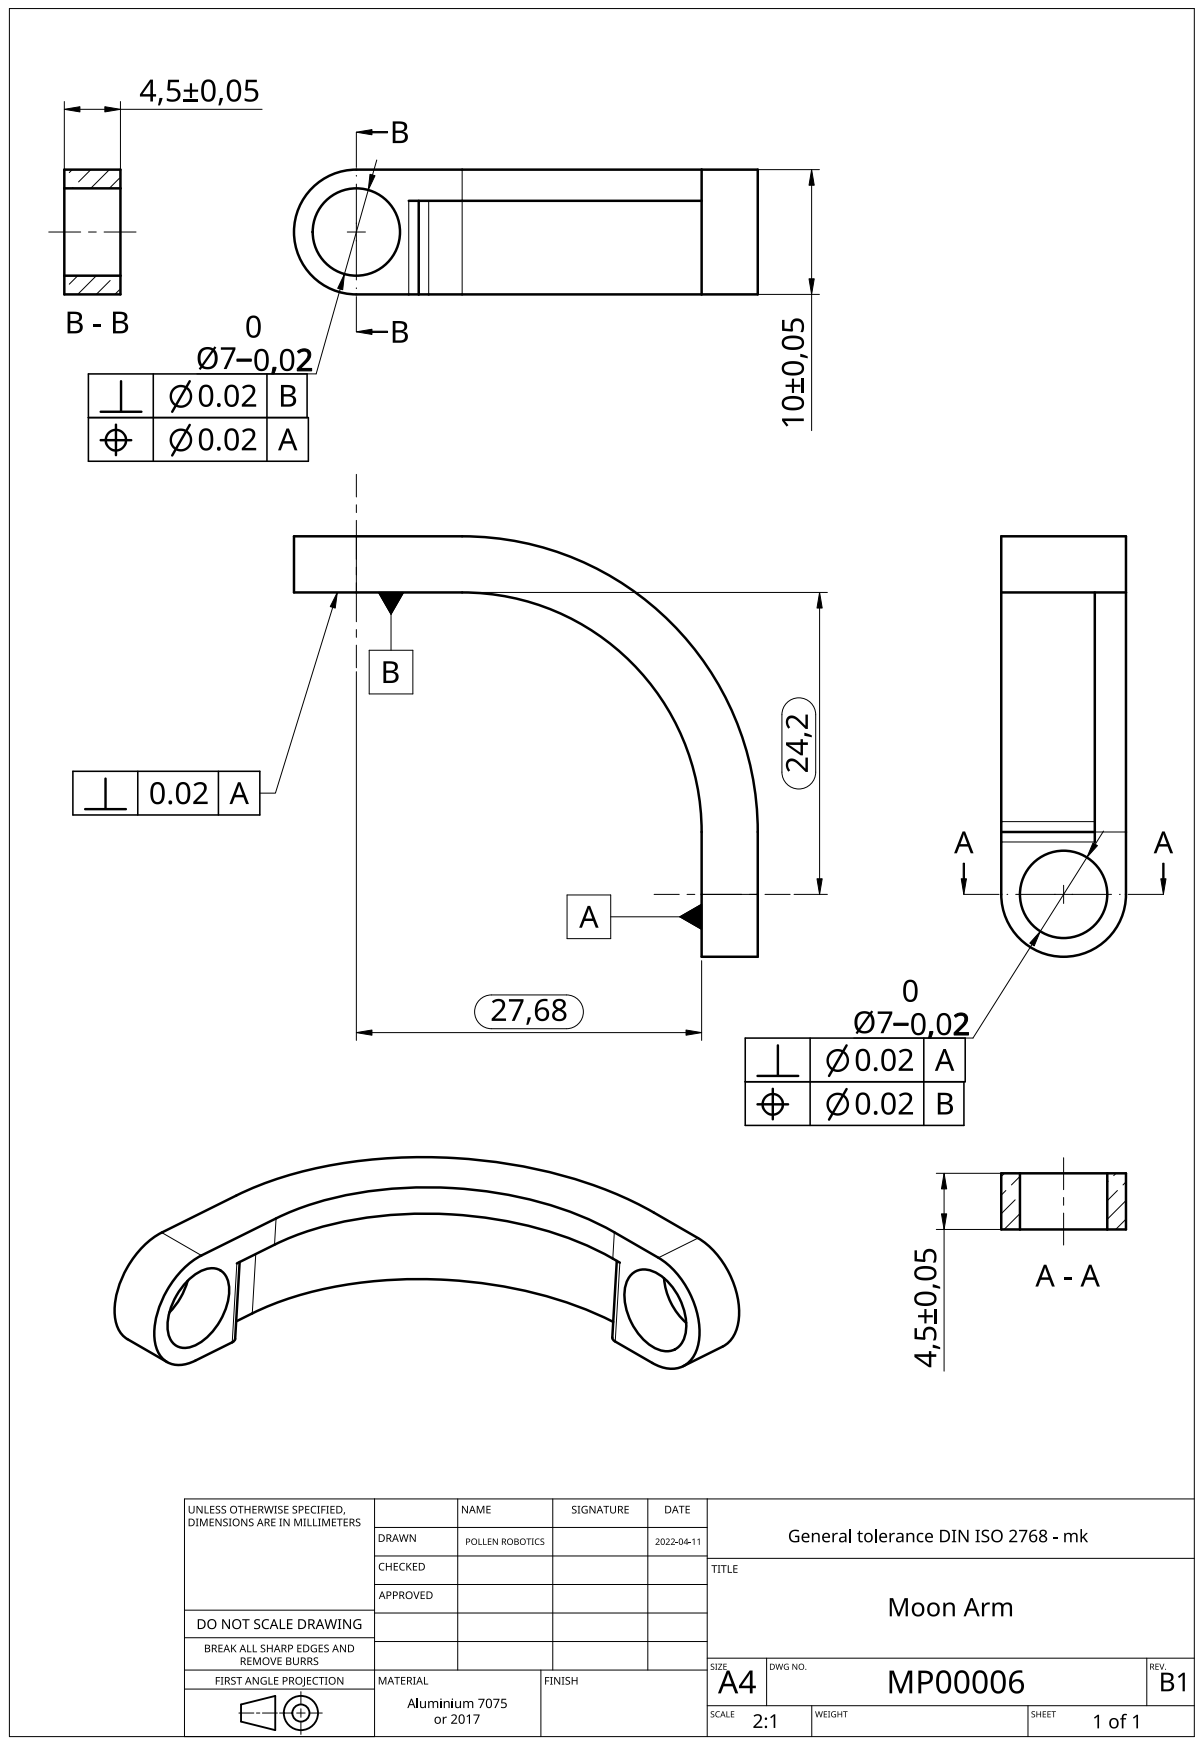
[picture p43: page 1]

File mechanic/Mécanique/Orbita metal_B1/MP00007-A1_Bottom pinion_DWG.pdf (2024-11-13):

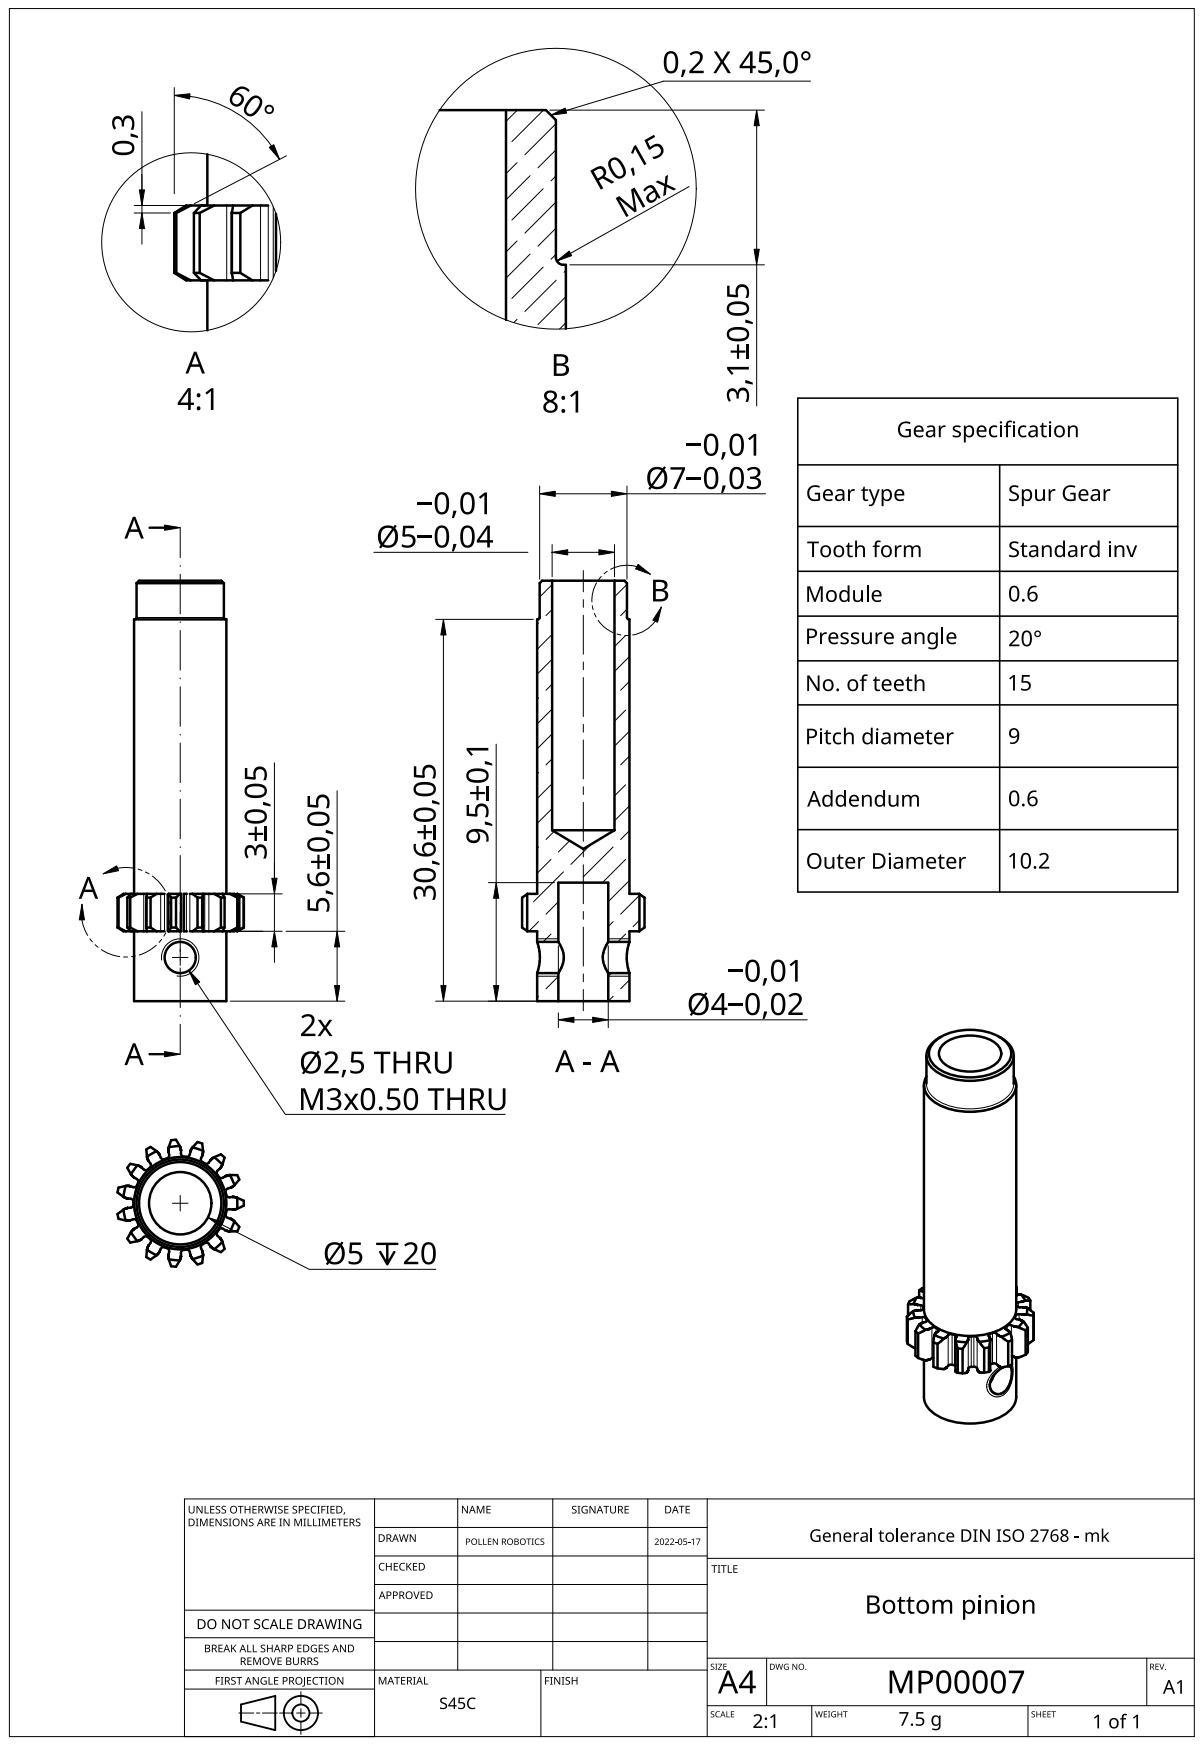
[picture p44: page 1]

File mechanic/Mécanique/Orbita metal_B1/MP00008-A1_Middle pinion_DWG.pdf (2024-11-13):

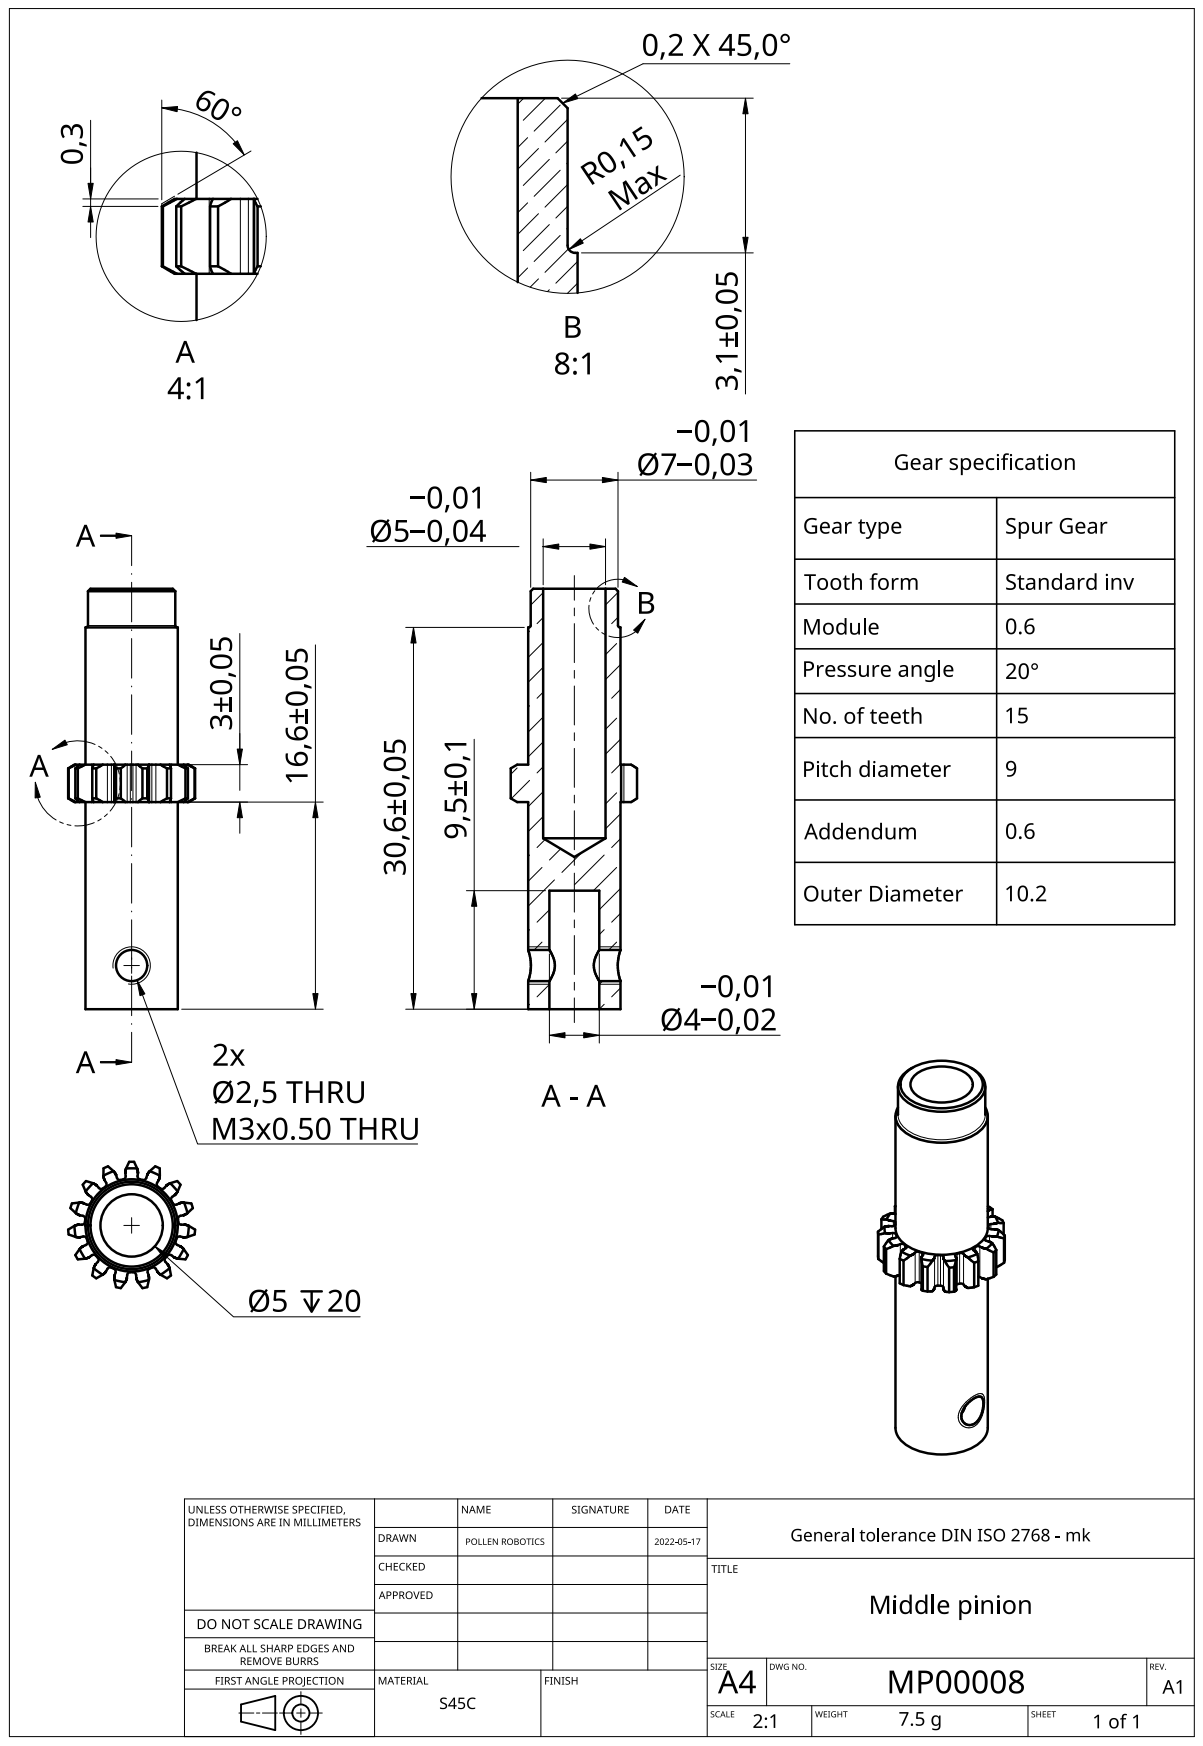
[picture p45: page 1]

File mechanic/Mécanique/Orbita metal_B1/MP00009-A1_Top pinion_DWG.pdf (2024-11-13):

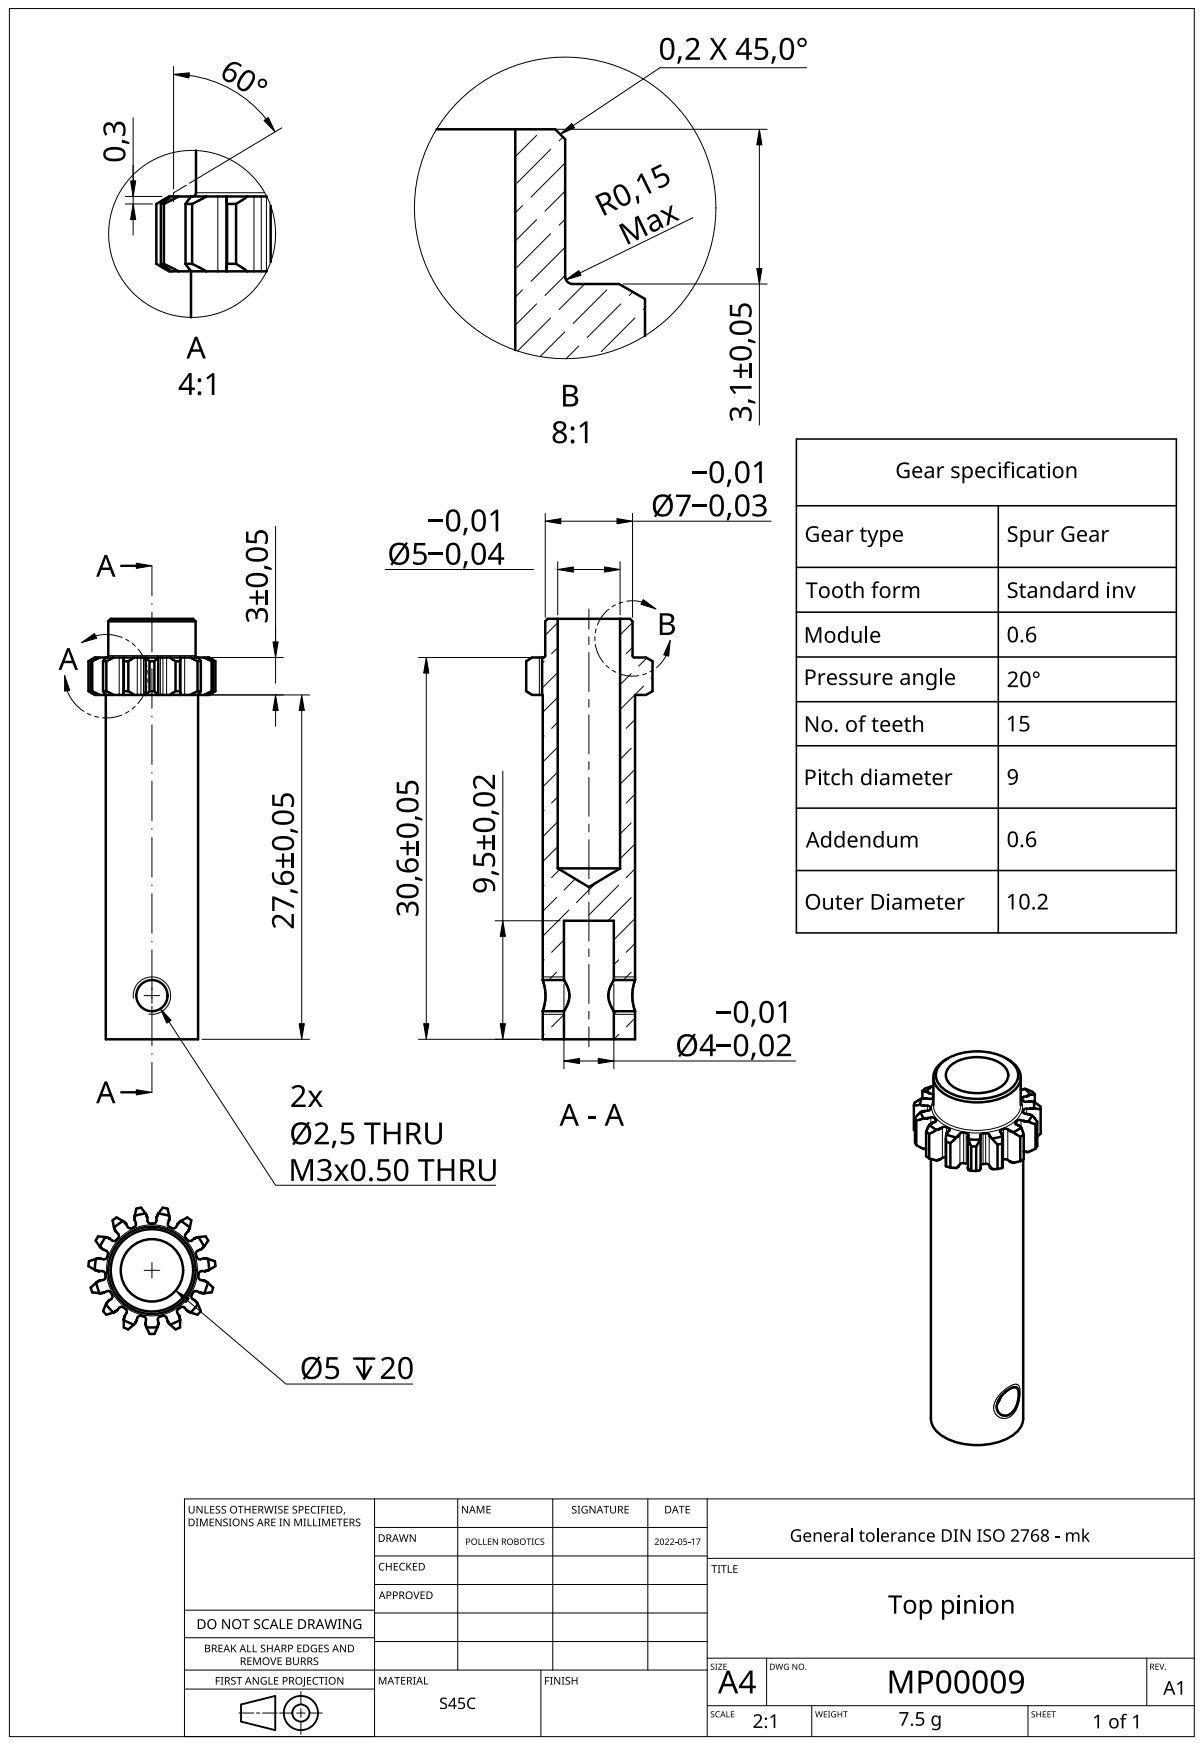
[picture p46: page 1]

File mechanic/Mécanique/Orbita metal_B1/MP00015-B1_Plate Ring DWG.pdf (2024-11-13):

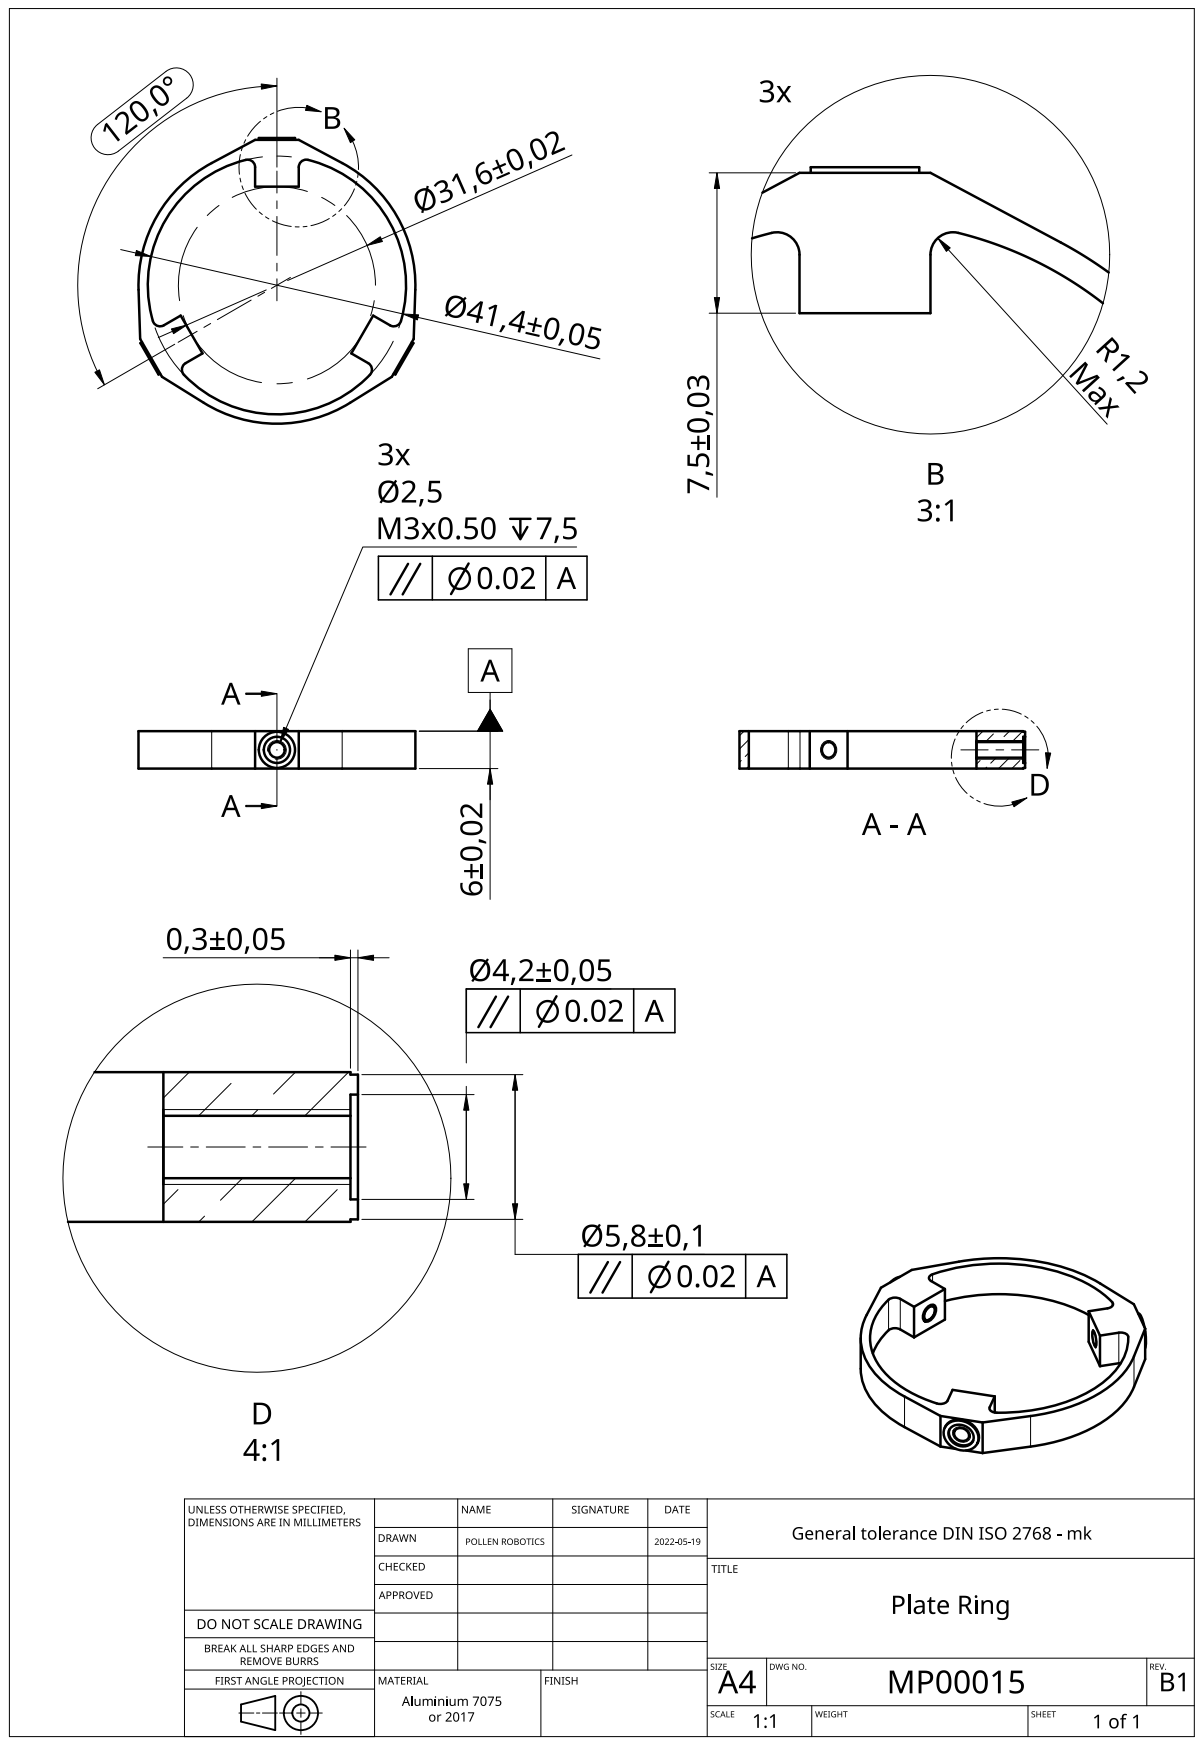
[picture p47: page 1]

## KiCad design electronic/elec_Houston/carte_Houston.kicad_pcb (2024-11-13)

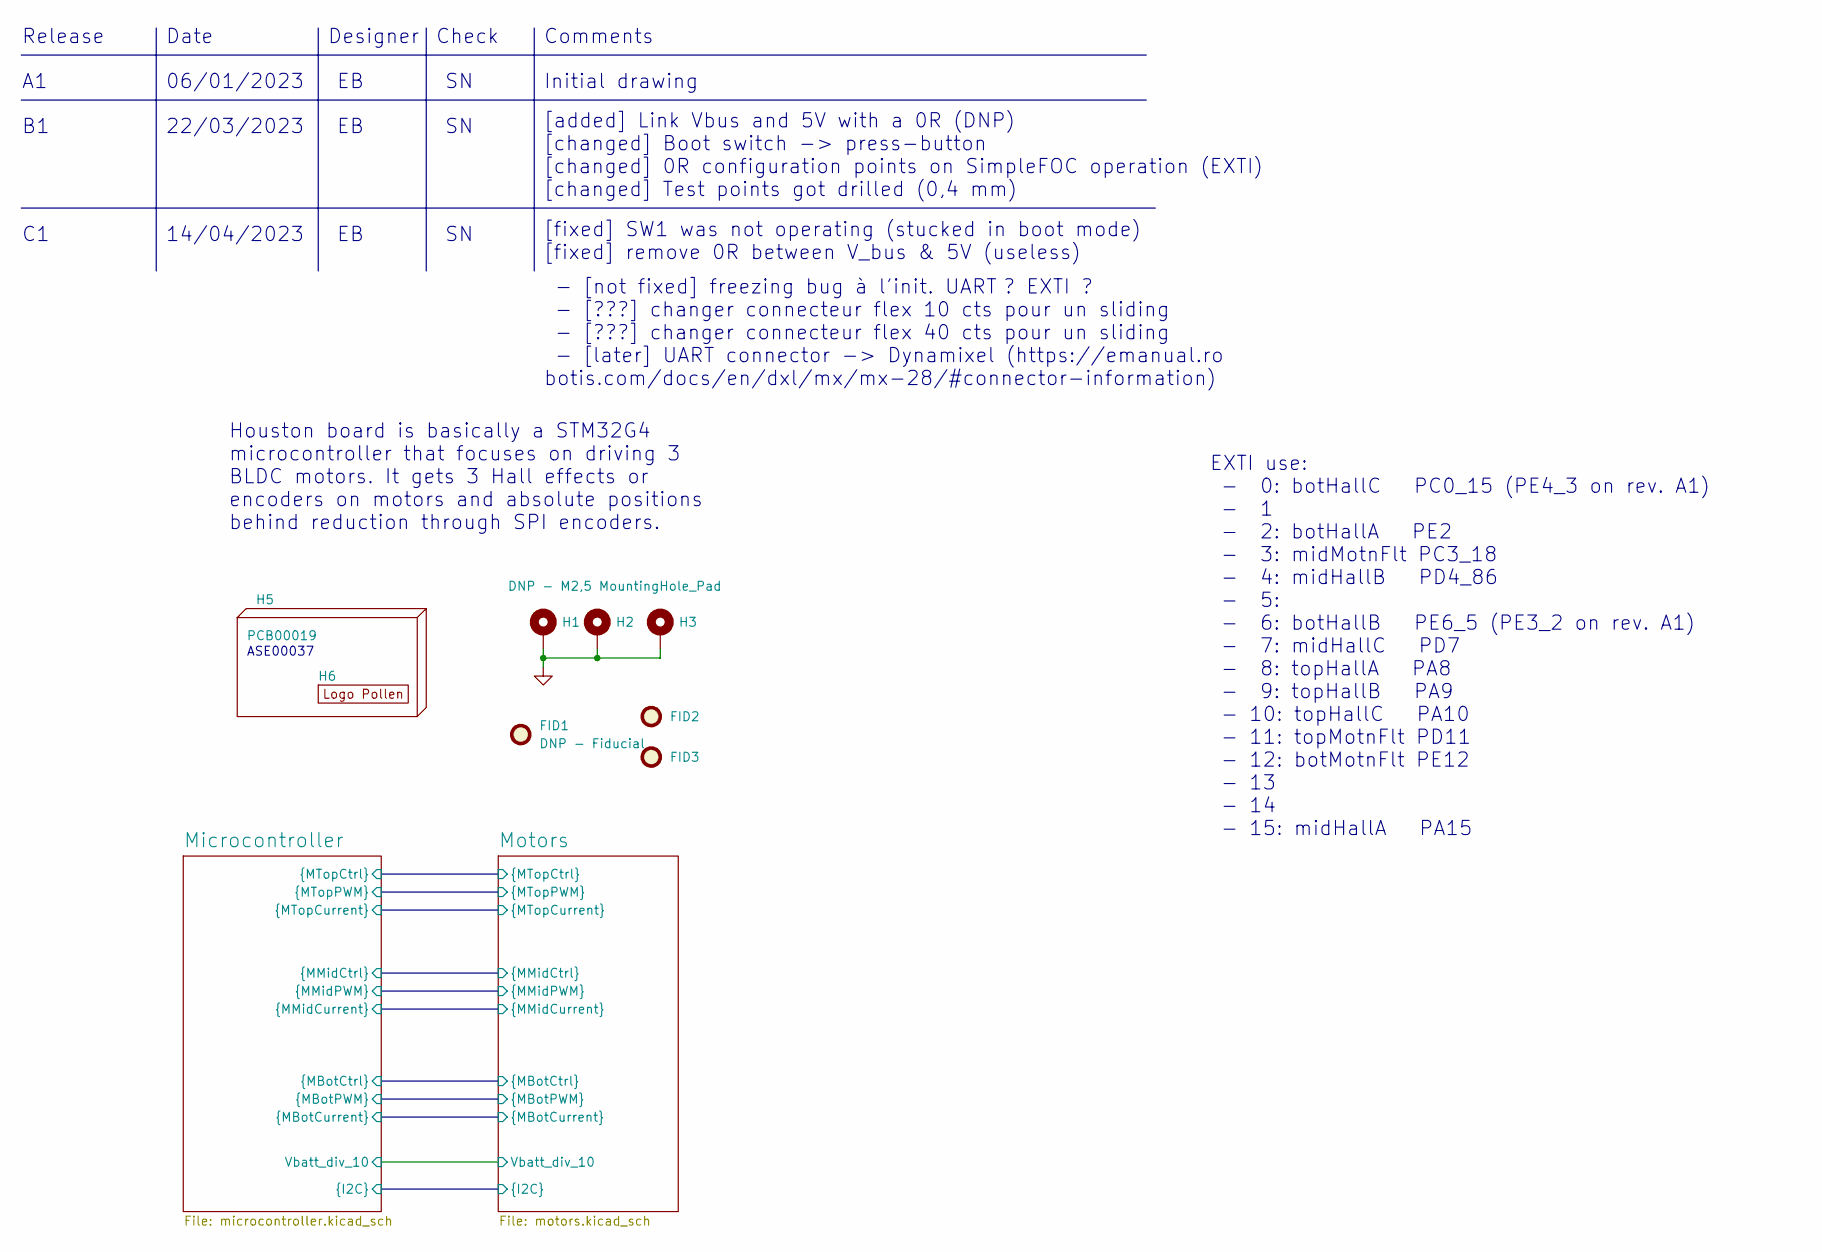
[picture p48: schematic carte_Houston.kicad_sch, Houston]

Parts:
FID1, FID2, FID3: DNP - Fiducial; Fiducial_1mm_Mask2mm
H1, H2, H3: DNP - M2,5 MountingHole_Pad; MountingHole_2.7mm_M2.5_DIN965_Pad_TopOnly
H5: PCB00019
H6: DNP - Logo Pollen 2021; Logo_Pollen_2021

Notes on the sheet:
Date
Check
Release
[added] Link Vbus and 5V with a 0R (DNP) [changed] Boot switch -> press-button [changed] 0R configuration points on SimpleFOC operation (EXTI) [changed] Test points got drilled (0,4 mm)
ASE00037
22/03/2023
- [not fixed] freezing bug à l'init. UART ? EXTI ? - [???] changer connecteur flex 10 cts pour un sliding - [???] changer connecteur flex 40 cts pour un sliding - [later] UART connector -> Dynamixel (https://emanual.ro botis.com/docs/en/dxl/mx/mx-28/#connector-information)
Initial drawing
[fixed] SW1 was not operating (stucked in boot mode) [fixed] remove 0R between V_bus & 5V (useless)
EXTI use: - 0: botHallC PC0_15 (PE4_3 on rev. A1) - 1 - 2: botHallA PE2 - 3: midMotnFlt PC3_18 - 4: midHallB PD4_86 - 5: - 6: botHallB PE6_5 (PE3_2 on rev. A1) - 7: midHallC PD7 - 8: topHallA PA8 - 9: topHallB PA9 - 10: topHallC PA10 - 11: topMotnFlt PD11 - 12: botMotnFlt PE12 - 13 - 14 - 15: midHa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
Designer
14/04/2023
Houston board is basically a STM32G4 microcontroller that focuses on driving 3 BLDC motors. It gets 3 Hall effects or encoders on motors and absolute positions behind reduction through SPI encoders.
Comments
06/01/2023

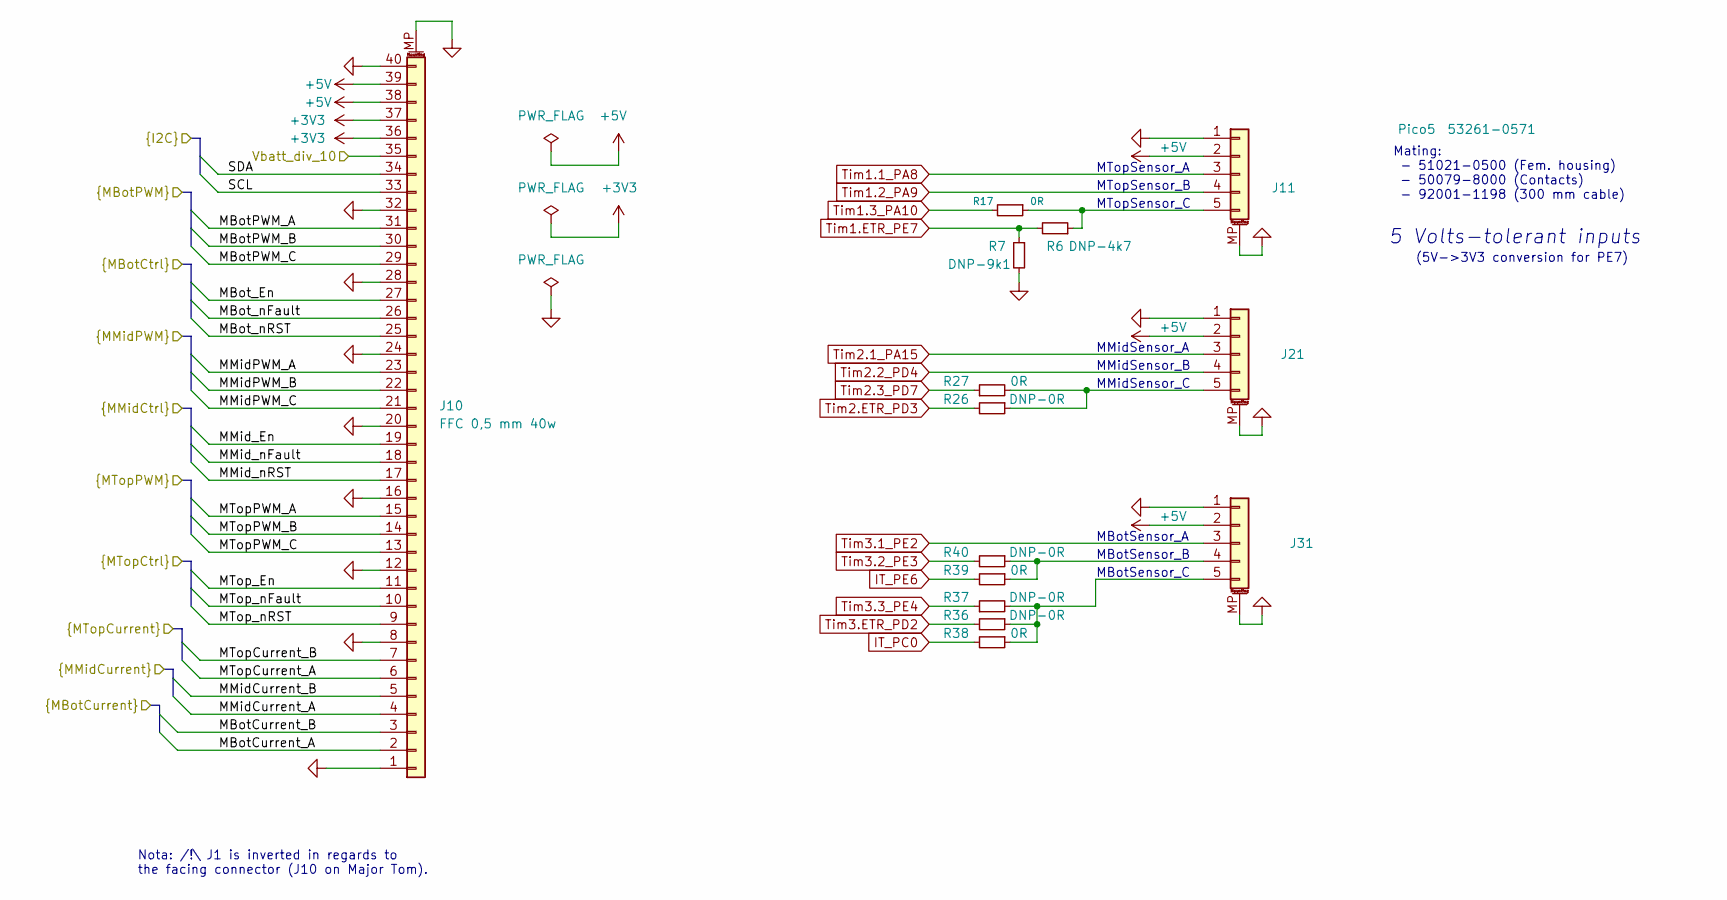
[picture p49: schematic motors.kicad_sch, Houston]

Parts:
J10: FFC 0,5 mm 40w; Hirose_FH12-40S-0.5SH_1x40-1MP_P0.50mm_Horizontal
J11: PicoBlade5; Molex_PicoBlade_53261-0571_1x05-1MP_P1.25mm_Horizontal
J21, J31: Pico5; Molex_PicoBlade_53261-0571_1x05-1MP_P1.25mm_Horizontal
R6: DNP-4k7; R_0603_1608Metric
R7: DNP-9k1; R_0603_1608Metric
R17, R27, R38, R39: 0R; R_0603_1608Metric
R26, R36, R37, R40: DNP-0R; R_0603_1608Metric

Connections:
+5V: J10.38, J10.39, J11.2, J21.2, J31.2
/Microcontroller/MBotCurrent_A: J10.2; also elsewhere on the board
/Microcontroller/MBotCurrent_B: J10.3; also elsewhere on the board
/Microcontroller/MBotPWM_A: J10.31; also elsewhere on the board
/Microcontroller/MBotPWM_B: J10.30; also elsewhere on the board
/Microcontroller/MBotPWM_C: J10.29; also elsewhere on the board
/Microcontroller/MBot_En: J10.27; also elsewhere on the board
/Microcontroller/MBot_nFault: J10.26; also elsewhere on the board
/Microcontroller/MBot_nRST: J10.25; also elsewhere on the board
/Microcontroller/MMidCurrent_A: J10.4; also elsewhere on the board
/Microcontroller/MMidCurrent_B: J10.5; also elsewhere on the board
/Microcontroller/MMidPWM_A: J10.23; also elsewhere on the board
/Microcontroller/MMidPWM_B: J10.22; also elsewhere on the board
/Microcontroller/MMidPWM_C: J10.21; also elsewhere on the board
/Microcontroller/MMid_En: J10.19; also elsewhere on the board
/Microcontroller/MMid_nFault: J10.18; also elsewhere on the board
/Microcontroller/MMid_nRST: J10.17; also elsewhere on the board
/Microcontroller/MTopCurrent_A: J10.6; also elsewhere on the board
/Microcontroller/MTopCurrent_B: J10.7; also elsewhere on the board
/Microcontroller/MTopPWM_A: J10.15; also elsewhere on the board
/Microcontroller/MTopPWM_B: J10.14; also elsewhere on the board
/Microcontroller/MTopPWM_C: J10.13; also elsewhere on the board
/Microcontroller/MTop_En: J10.11; also elsewhere on the board
/Microcontroller/MTop_nFault: J10.10; also elsewhere on the board
/Microcontroller/MTop_nRST: J10.9; also elsewhere on the board
/Microcontroller/SCL: J10.33; also elsewhere on the board
/Microcontroller/SDA: J10.34; also elsewhere on the board
/Microcontroller/Vbatt_div_10: J10.35; also elsewhere on the board
IT_PC0: R38.2; also elsewhere on the board
IT_PE6: R39.2; also elsewhere on the board
unnamed: J11.5, R6.1, R17.1
unnamed: J21.5, R26.1, R27.2
unnamed: J31.4, R39.1, R40.1
unnamed: J31.5, R36.1, R37.2, R38.1
Tim1.1_PA8: J11.3; also elsewhere on the board
Tim1.2_PA9: J11.4; also elsewhere on the board
Tim1.3_PA10: R17.2; also elsewhere on the board
Tim1.ETR_PE7: R6.2, R7.1; also elsewhere on the board
Tim2.1_PA15: J21.3; also elsewhere on the board
Tim2.2_PD4: J21.4; also elsewhere on the board
Tim2.3_PD7: R27.1; also elsewhere on the board
Tim2.ETR_PD3: R26.2; also elsewhere on the board
Tim3.1_PE2: J31.3; also elsewhere on the board
Tim3.2_PE3: R40.2; also elsewhere on the board
Tim3.3_PE4: R37.1; also elsewhere on the board
Tim3.ETR_PD2: R36.2; also elsewhere on the board

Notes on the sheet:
MTopSensor_B
MBotSensor_A
MBotSensor_C
MTopSensor_C
MMidSensor_A
(5V->3V3 conversion for PE7)
MBotSensor_B
MTopSensor_A
MMidSensor_B
5 Volts-tolerant inputs
Nota: /!\ J1 is inverted in regards to the facing connector (J10 on Major Tom).
Mating: - 51021-0500 (Fem. housing) - 50079-8000 (Contacts) - 92001-1198 (300 mm cable)
MMidSensor_C

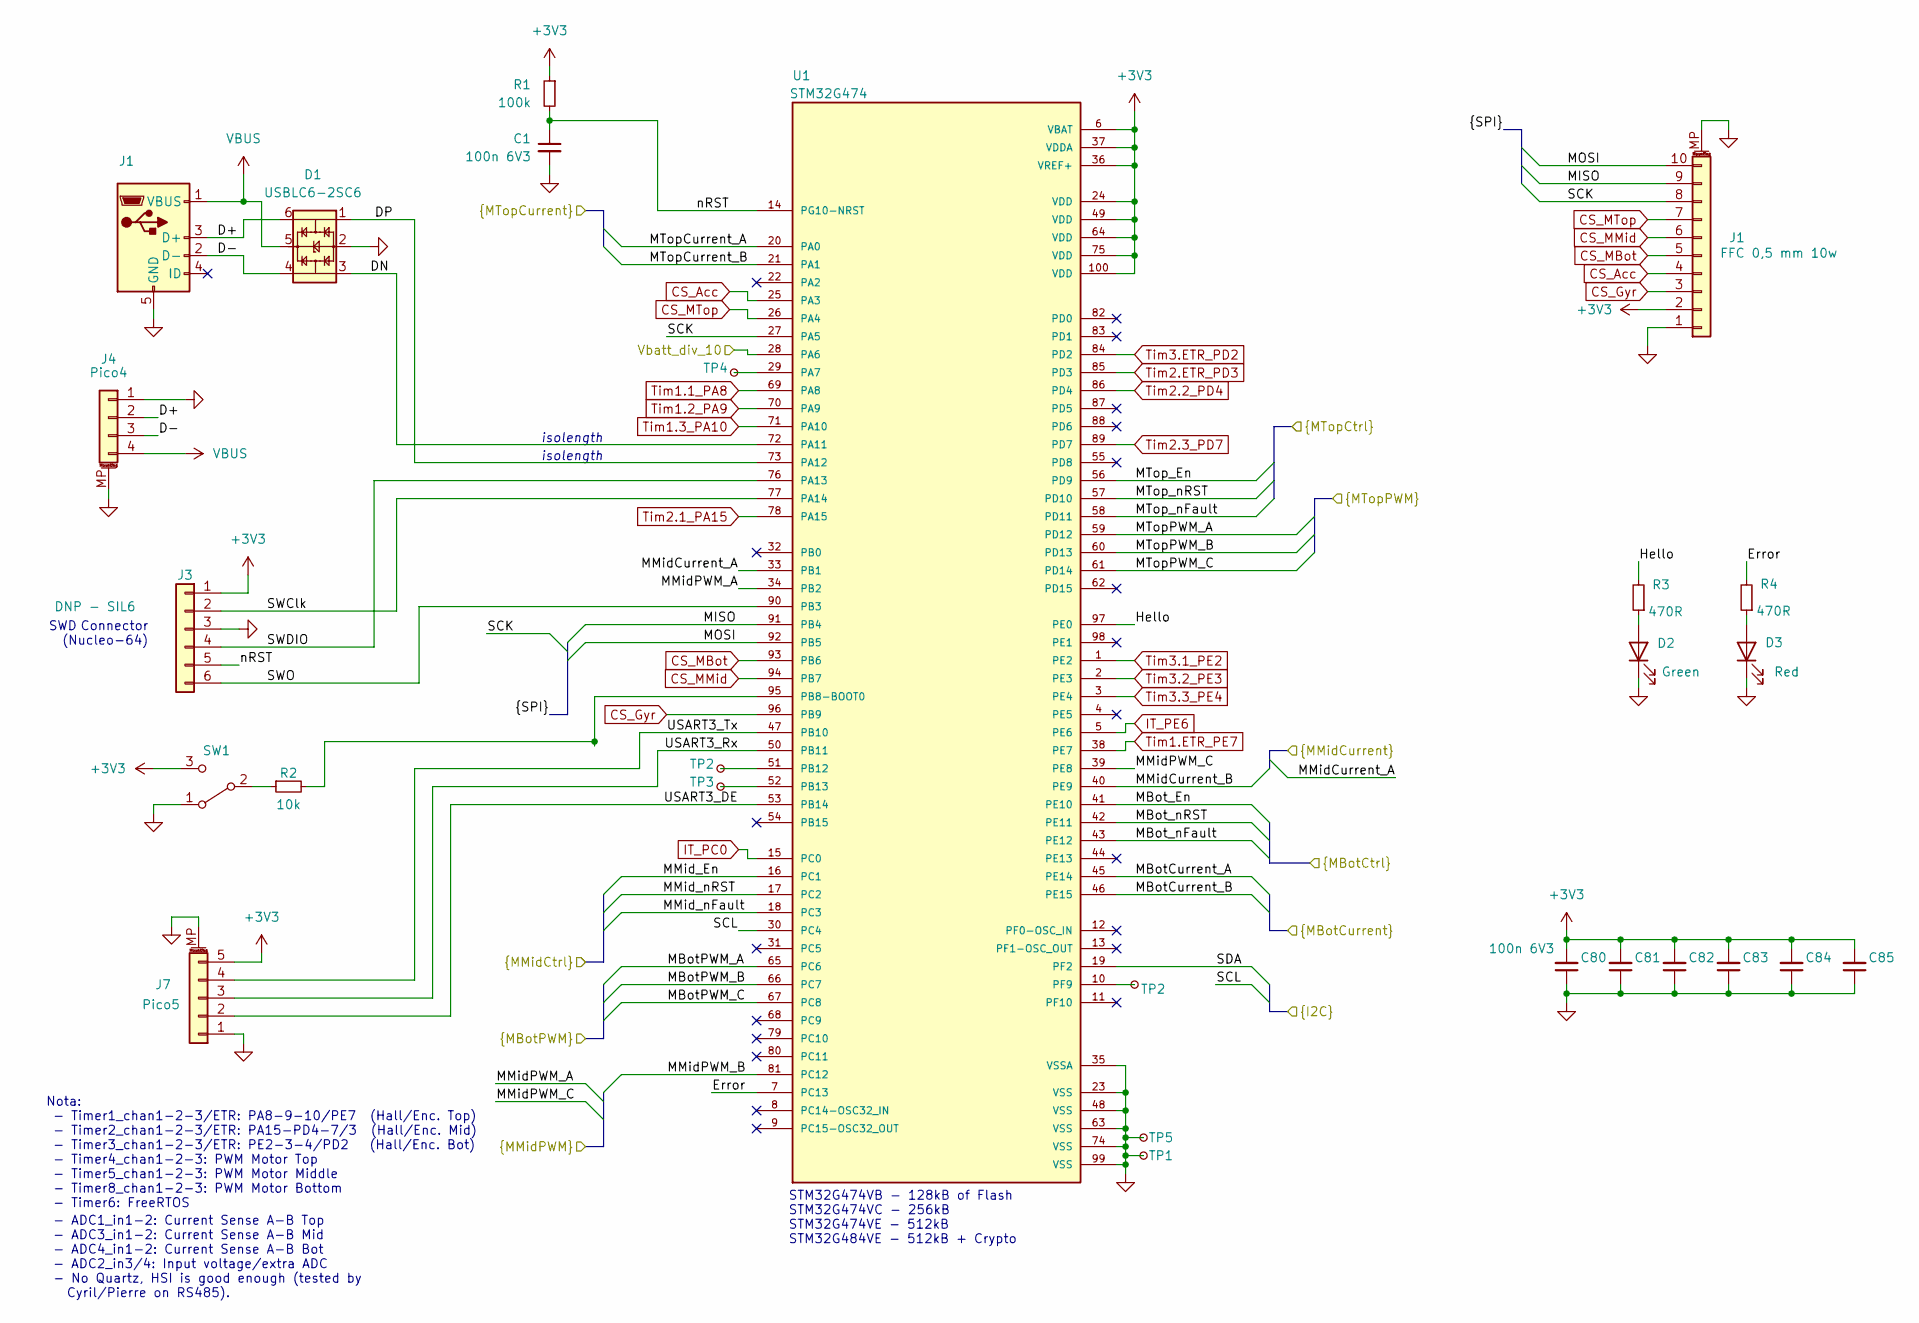
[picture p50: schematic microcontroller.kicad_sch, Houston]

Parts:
C1, C80, C81, C82, C83, C84, C85: 100n 6V3; C_0603_1608Metric
D1: USBLC6-2SC6; SOT23-6L
D2: Green; LED_0603_1608Metric_Pad1.05x0.95mm_HandSolder
D3: Red; LED_0603_1608Metric_Pad1.05x0.95mm_HandSolder
J1: 10118194-0001LF; Amphenol_10118194-0001LF
J3: SIL6; PinHeader_1x06_P2.54mm_Vertical_SMD_Pin1Left
J4: PicoBlade4; Molex_PicoBlade_53398-0471_1x04-1MP_P1.25mm_Vertical
J7: PicoBlade5; Molex_PicoBlade_53261-0571_1x05-1MP_P1.25mm_Horizontal
R1: 100k; R_0603_1608Metric
R2: 10k; R_0603_1608Metric
R3, R4: 470R; R_0603_1608Metric
SW1: SW_SPDT; SW_SPDT_CK-JS102011SAQN
TP1: DNP TestPoint_Small; TestPoint_THTPad_2.0x2.0mm_Drill1.0mm
TP2: DNP TestPoint_Small; TestPoint_Pad_D1.0mm
TP3, TP4, TP5: DNP - TestPoint_Small; TestPoint_THTPad_D1.0mm_Drill0.4mm
U1: STM32G474; QFP50P1600X1600X160-100N

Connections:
/Microcontroller/DN: D1.3, U1.72 (PA11)
/Microcontroller/DP: D1.1, U1.73 (PA12)
/Microcontroller/Error: R4.2, U1.7 (PC13)
/Microcontroller/Hello: R3.2, U1.97 (PE0)
/Microcontroller/MBotCurrent_A: U1.45 (PE14); also elsewhere on the board
/Microcontroller/MBotCurrent_B: U1.46 (PE15); also elsewhere on the board
/Microcontroller/MBotPWM_A: U1.65 (PC6); also elsewhere on the board
/Microcontroller/MBotPWM_B: U1.66 (PC7); also elsewhere on the board
/Microcontroller/MBotPWM_C: U1.67 (PC8); also elsewhere on the board
/Microcontroller/MBot_En: U1.41 (PE10); also elsewhere on the board
/Microcontroller/MBot_nFault: U1.43 (PE12); also elsewhere on the board
/Microcontroller/MBot_nRST: U1.42 (PE11); also elsewhere on the board
/Microcontroller/MISO: J1.9, U1.91 (PB4)
/Microcontroller/MMidCurrent_A: U1.33 (PB1); also elsewhere on the board
/Microcontroller/MMidCurrent_B: U1.40 (PE9); also elsewhere on the board
/Microcontroller/MMidPWM_A: U1.34 (PB2); also elsewhere on the board
/Microcontroller/MMidPWM_B: U1.81 (PC12); also elsewhere on the board
/Microcontroller/MMidPWM_C: U1.39 (PE8); also elsewhere on the board
/Microcontroller/MMid_En: U1.16 (PC1); also elsewhere on the board
/Microcontroller/MMid_nFault: U1.18 (PC3); also elsewhere on the board
/Microcontroller/MMid_nRST: U1.17 (PC2); also elsewhere on the board
/Microcontroller/MOSI: J1.10, U1.92 (PB5)
/Microcontroller/MTopCurrent_A: U1.20 (PA0); also elsewhere on the board
/Microcontroller/MTopCurrent_B: U1.21 (PA1); also elsewhere on the board
/Microcontroller/MTopPWM_A: U1.59 (PD12); also elsewhere on the board
/Microcontroller/MTopPWM_B: U1.60 (PD13); also elsewhere on the board
/Microcontroller/MTopPWM_C: U1.61 (PD14); also elsewhere on the board
/Microcontroller/MTop_En: U1.56 (PD9); also elsewhere on the board
/Microcontroller/MTop_nFault: U1.58 (PD11); also elsewhere on the board
/Microcontroller/MTop_nRST: U1.57 (PD10); also elsewhere on the board
/Microcontroller/SCK: J1.8, U1.27 (PA5)
/Microcontroller/SCL: U1.30 (PC4); also elsewhere on the board
/Microcontroller/SDA: U1.19 (PF2); also elsewhere on the board
/Microcontroller/SWClk: J3.2, U1.77 (PA14)
/Microcontroller/SWDIO: J3.4, U1.76 (PA13)
/Microcontroller/SWO: J3.6, U1.90 (PB3)
/Microcontroller/USART3_DE: J7.2, U1.53 (PB14)
/Microcontroller/USART3_Rx: J7.3, U1.50 (PB11)
/Microcontroller/USART3_Tx: J7.4, U1.47 (PB10)
/Microcontroller/Vbatt_div_10: U1.28 (PA6); also elsewhere on the board
/Microcontroller/nRST: C1.1, J3.5, R1.2, U1.14 (PG10-NRST)
CS_Acc: J1.4, U1.25 (PA3)
CS_MMid: J1.6, U1.94 (PB7)
CS_MTop: J1.7, U1.26 (PA4)
IT_PC0: U1.15 (PC0); also elsewhere on the board
IT_PE6: U1.5 (PE6); also elsewhere on the board
unnamed: D2.2 (A), R3.1
unnamed: D3.2 (A), R4.1
unnamed: R2.1, SW1.2 (B)
unnamed: R2.2, U1.95 (PB8-BOOT0)
unnamed: TP3.1, U1.52 (PB13)
unnamed: TP4.1, U1.29 (PA7)
Tim1.1_PA8: U1.69 (PA8); also elsewhere on the board
Tim1.2_PA9: U1.70 (PA9); also elsewhere on the board
Tim1.3_PA10: U1.71 (PA10); also elsewhere on the board
Tim1.ETR_PE7: U1.38 (PE7); also elsewhere on the board
Tim2.1_PA15: U1.78 (PA15); also elsewhere on the board
Tim2.2_PD4: U1.86 (PD4); also elsewhere on the board
Tim2.3_PD7: U1.89 (PD7); also elsewhere on the board
Tim2.ETR_PD3: U1.85 (PD3); also elsewhere on the board
Tim3.1_PE2: U1.1 (PE2); also elsewhere on the board
Tim3.2_PE3: U1.2 (PE3); also elsewhere on the board
Tim3.3_PE4: U1.3 (PE4); also elsewhere on the board
Tim3.ETR_PD2: U1.84 (PD2); also elsewhere on the board

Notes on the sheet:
Nota: - Timer1_chan1-2-3/ETR: PA8-9-10/PE7 (Hall/Enc. Top) - Timer2_chan1-2-3/ETR: PA15-PD4-7/3 (Hall/Enc. Mid) - Timer3_chan1-2-3/ETR: PE2-3-4/PD2 (Hall/Enc. Bot) - Timer4_chan1-2-3: PWM Motor Top - Timer5_chan1-2-3: PWM Motor Middle - Timer8_chan1-2-3: PWM Motor Bottom - Timer6: FreeRTOS
isolength
STM32G474VB - 128kB of Flash STM32G474VC - 256kB STM32G474VE - 512kB STM32G484VE - 512kB + Crypto
SWD Connector (Nucleo-64)
- ADC1_in1-2: Current Sense A-B Top - ADC3_in1-2: Current Sense A-B Mid - ADC4_in1-2: Current Sense A-B Bot - ADC2_in3/4: Input voltage/extra ADC - No Quartz, HSI is good enough (tested by Cyril/Pierre on RS485).

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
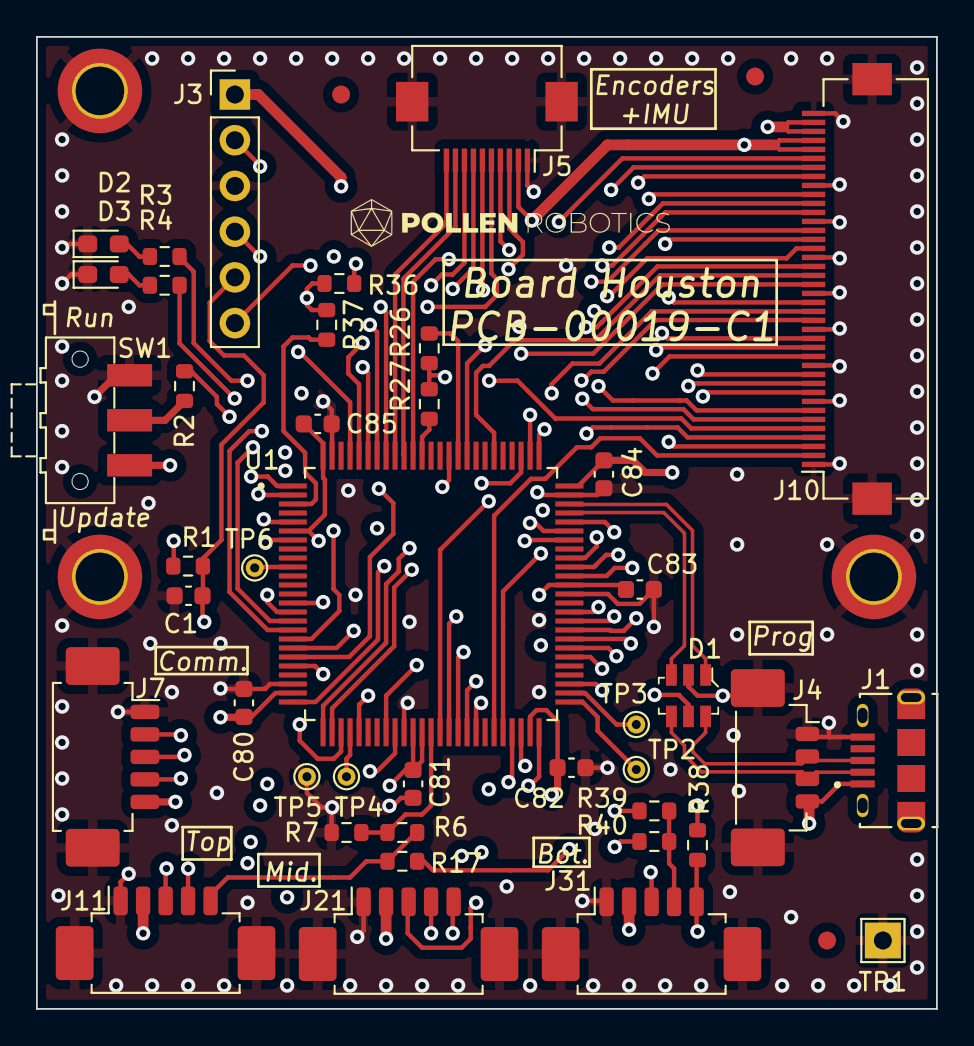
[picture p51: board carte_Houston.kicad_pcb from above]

Board: 4 copper layers, 50.0 x 54.0 mm, 48 parts (0 on the bottom side), 78 nets.

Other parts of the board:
J1#2: 10118194-0001LF; Amphenol_10118194-0001LF
TP2#2: DNP TestPoint_Small; TestPoint_THTPad_D1.0mm_Drill0.4mm

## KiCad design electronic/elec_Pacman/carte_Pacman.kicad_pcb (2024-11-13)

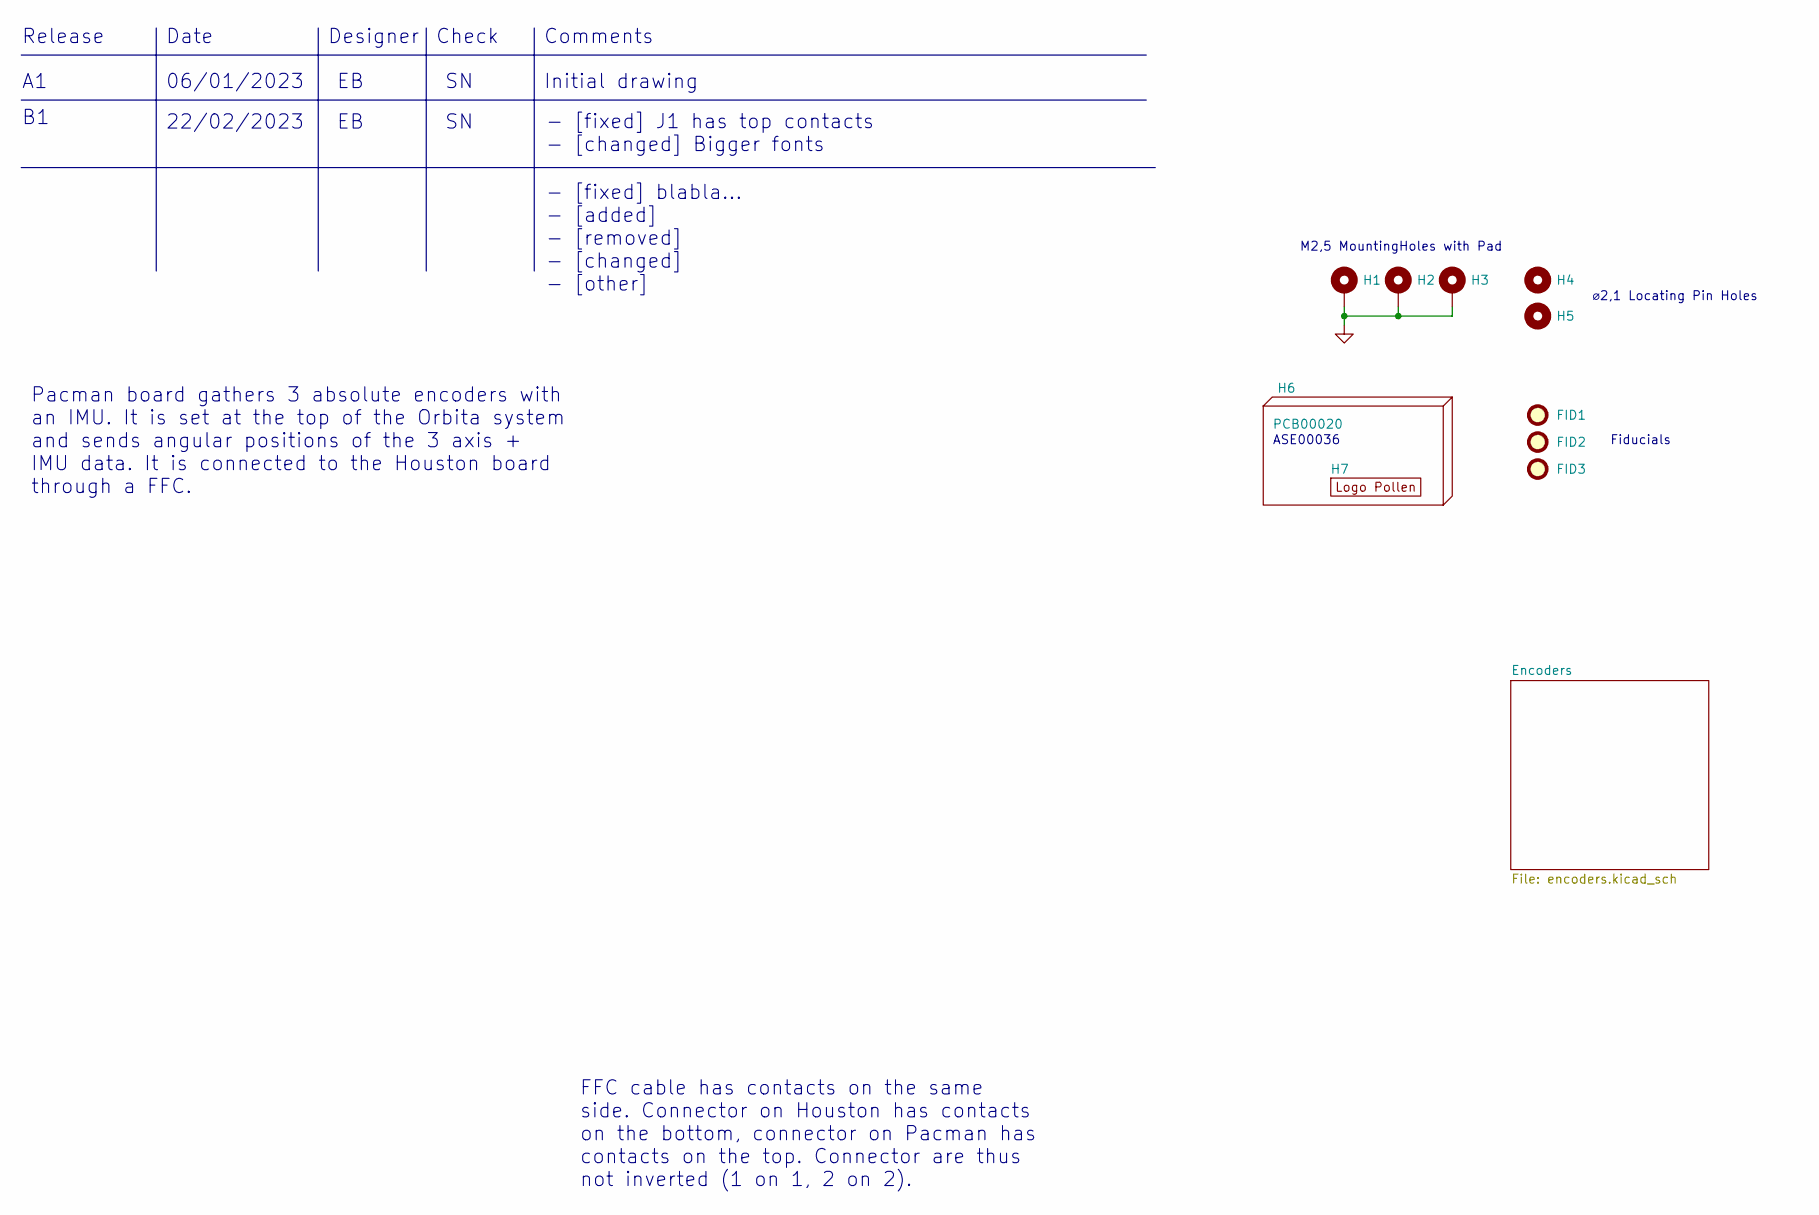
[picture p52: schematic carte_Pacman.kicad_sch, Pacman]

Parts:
FID1, FID2, FID3: DNP - Fiducial; Fiducial_0.5mm_Mask1mm
H1, H2: MountingHole_Pad; MountingHole_2.7mm_M2.5_DIN965_Pad_TopBottom
H3: DNP - MountingHole_Pad; MountingHole_2.7mm_M2.5_DIN965_Pad_TopBottom
H4, H5: DNP - LocatingPinHole; MountingHole_2.1mm
H6: PCB00020
H7: DNP Logo Pollen 2021; Logo_Pollen_2021

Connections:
GND: H1.1, H2.1, H3.1; also elsewhere on the board

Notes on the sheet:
M2,5 MountingHoles with Pad
Date
Check
Release
Fiducials
ASE00036
Pacman board gathers 3 absolute encoders with an IMU. It is set at the top of the Orbita system and sends angular positions of the 3 axis + IMU data. It is connected to the Houston board through a FFC.
22/02/2023
Initial drawing
FFC cable has contacts on the same side. Connector on Houston has contacts on the bottom, connector on Pacman has contacts on the top. Connector are thus not inverted (1 on 1, 2 on 2).
Designer
- [fixed] blabla... - [added] - [removed] - [changed] - [other]
- [fixed] J1 has top contacts - [changed] Bigger fonts
Comments
⌀2,1 Locating Pin Holes
06/01/2023

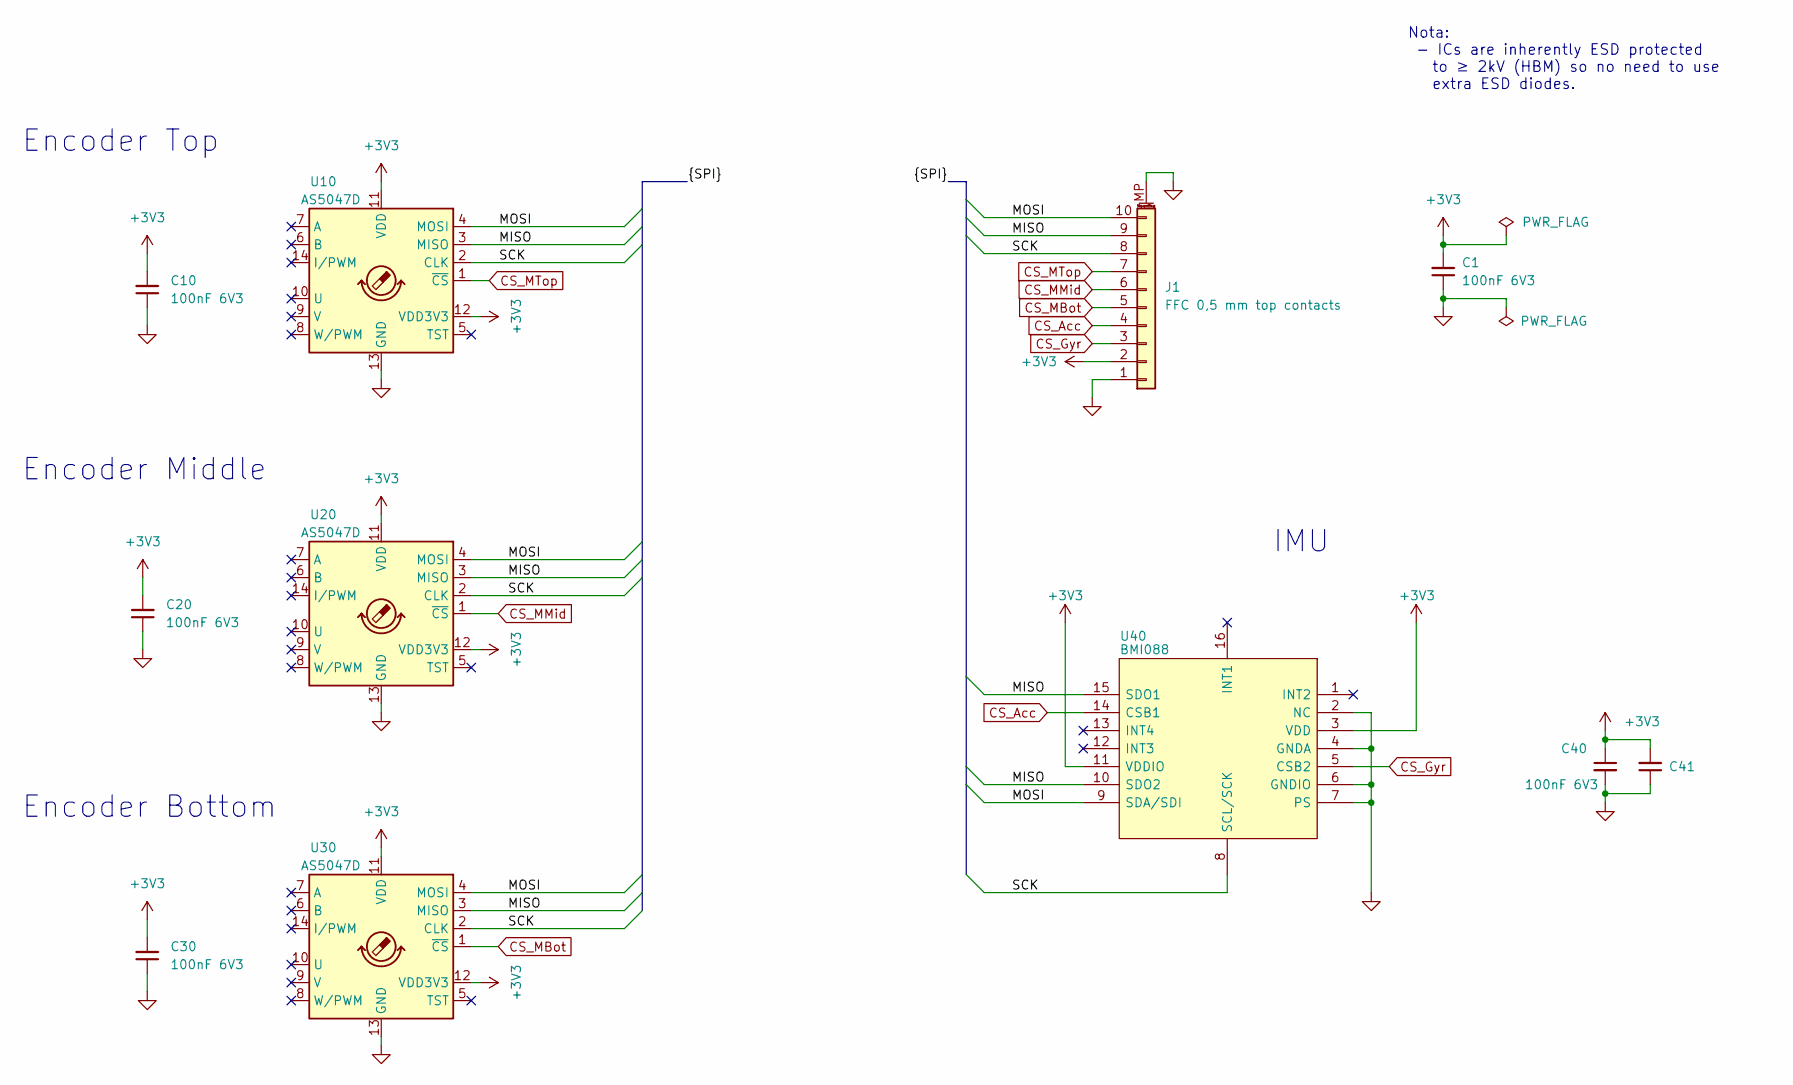
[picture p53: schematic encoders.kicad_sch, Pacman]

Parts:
C1, C10, C20, C30, C40, C41: 100nF 6V3; C_0603_1608Metric
J1: Conn_01x10_MountingPin; TE_1-1734839-0
U10, U20, U30: AS5047D; TSSOP-14_4.4x5mm_P0.65mm
U40: BMI088

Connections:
+3V3: C1.2, C10.2, C20.2, C30.2, C40.1, C41.2, J1.2, U10.11 (VDD), U10.12 (VDD3V3), U20.11 (VDD), U20.12 (VDD3V3), U30.11 (VDD), U30.12 (VDD3V3), U40.3 (VDD), U40.11 (VDDIO)
/Encoders/MISO: J1.9, U10.3 (MISO), U20.3 (MISO), U30.3 (MISO), U40.10 (SDO2), U40.15 (SDO1)
/Encoders/MOSI: J1.10, U10.4 (MOSI), U20.4 (MOSI), U30.4 (MOSI), U40.9 (SDA/SDI)
/Encoders/SCK: J1.8, U10.2 (CLK), U20.2 (CLK), U30.2 (CLK), U40.8 (SCL/SCK)
CS_Acc: J1.4, U40.14 (CSB1)
CS_Gyr: J1.3, U40.5 (CSB2)
CS_MBot: J1.5, U30.1 (~CS)
CS_MMid: J1.6, U20.1 (~CS)
CS_MTop: J1.7, U10.1 (~CS)
GND: C1.1, C10.1, C20.1, C30.1, C40.2, C41.1, J1.1, J1.MP (MountPin), U10.13 (GND), U20.13 (GND), U30.13 (GND), U40.2 (NC), U40.4 (GNDA), U40.6 (GNDIO), U40.7 (PS); also elsewhere on the board

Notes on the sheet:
Nota: - ICs are inherently ESD protected to ≥ 2kV (HBM) so no need to use extra ESD diodes.
Encoder Top
Encoder Middle
IMU
Encoder Bottom

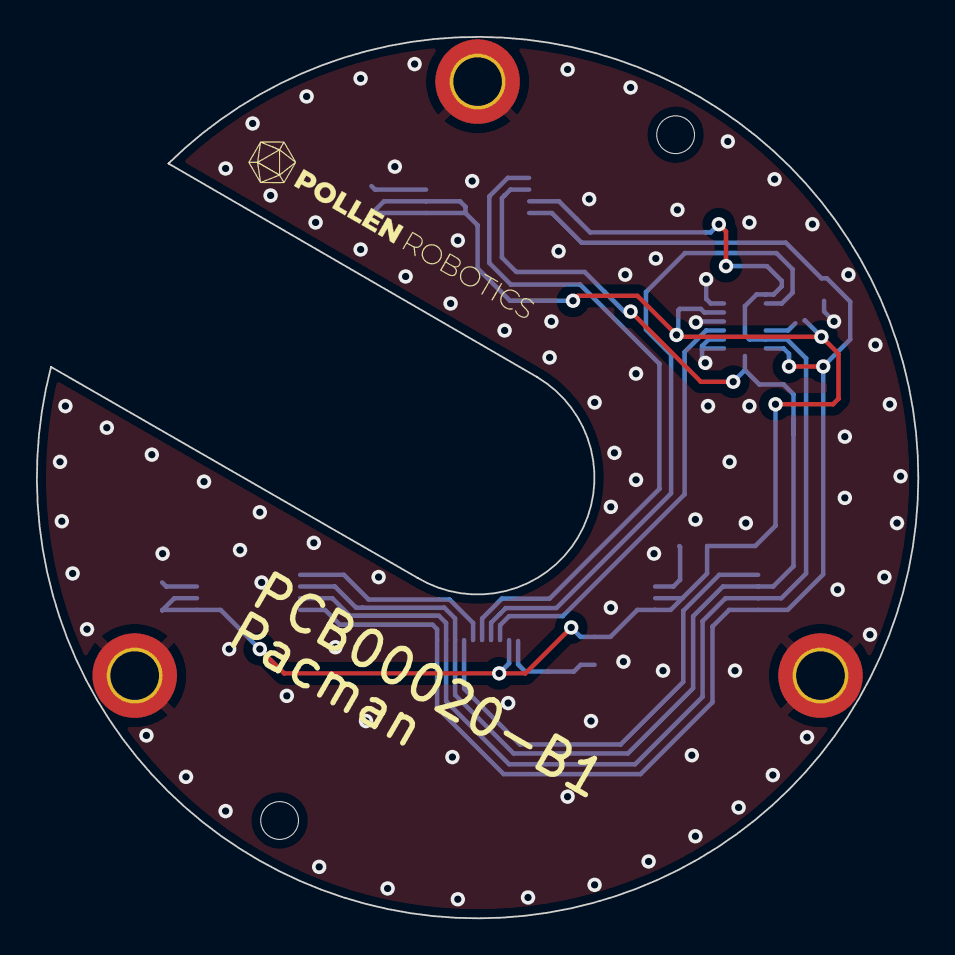
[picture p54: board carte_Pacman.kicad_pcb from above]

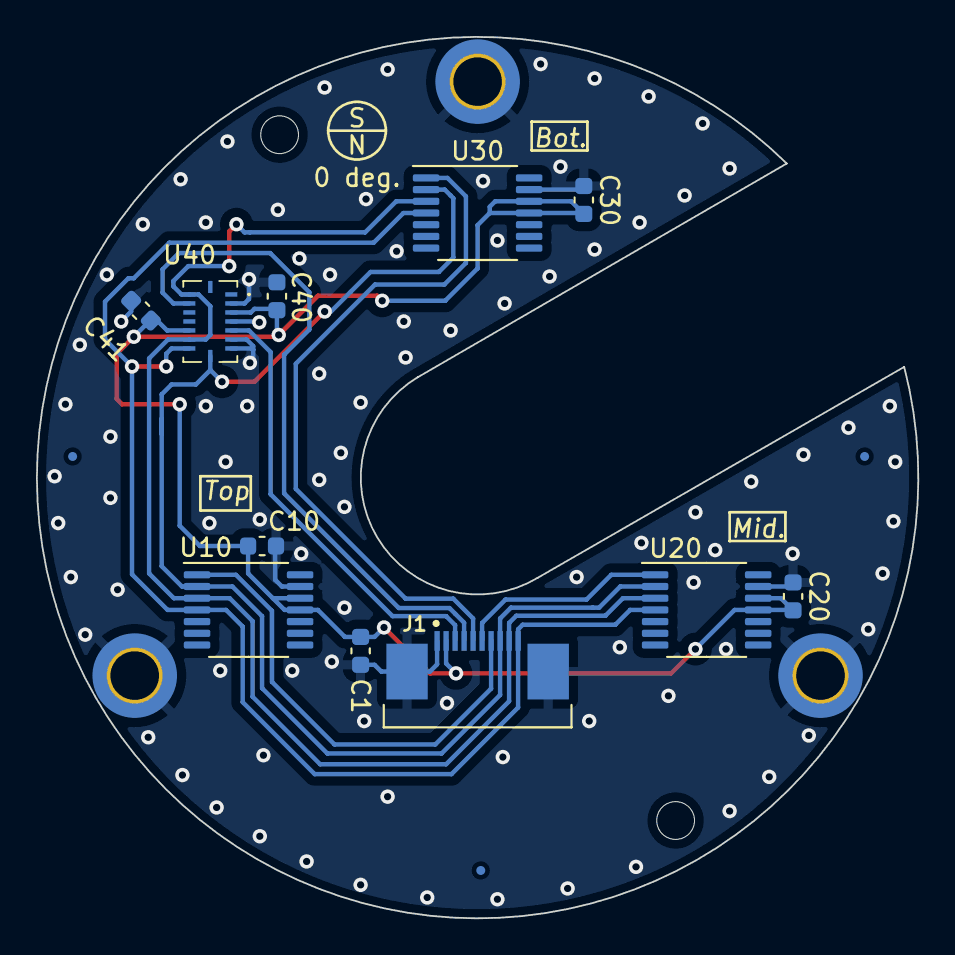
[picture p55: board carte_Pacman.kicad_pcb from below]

Board: 2 copper layers, 49.0 x 49.0 mm, 20 parts (14 on the bottom side), 10 nets.

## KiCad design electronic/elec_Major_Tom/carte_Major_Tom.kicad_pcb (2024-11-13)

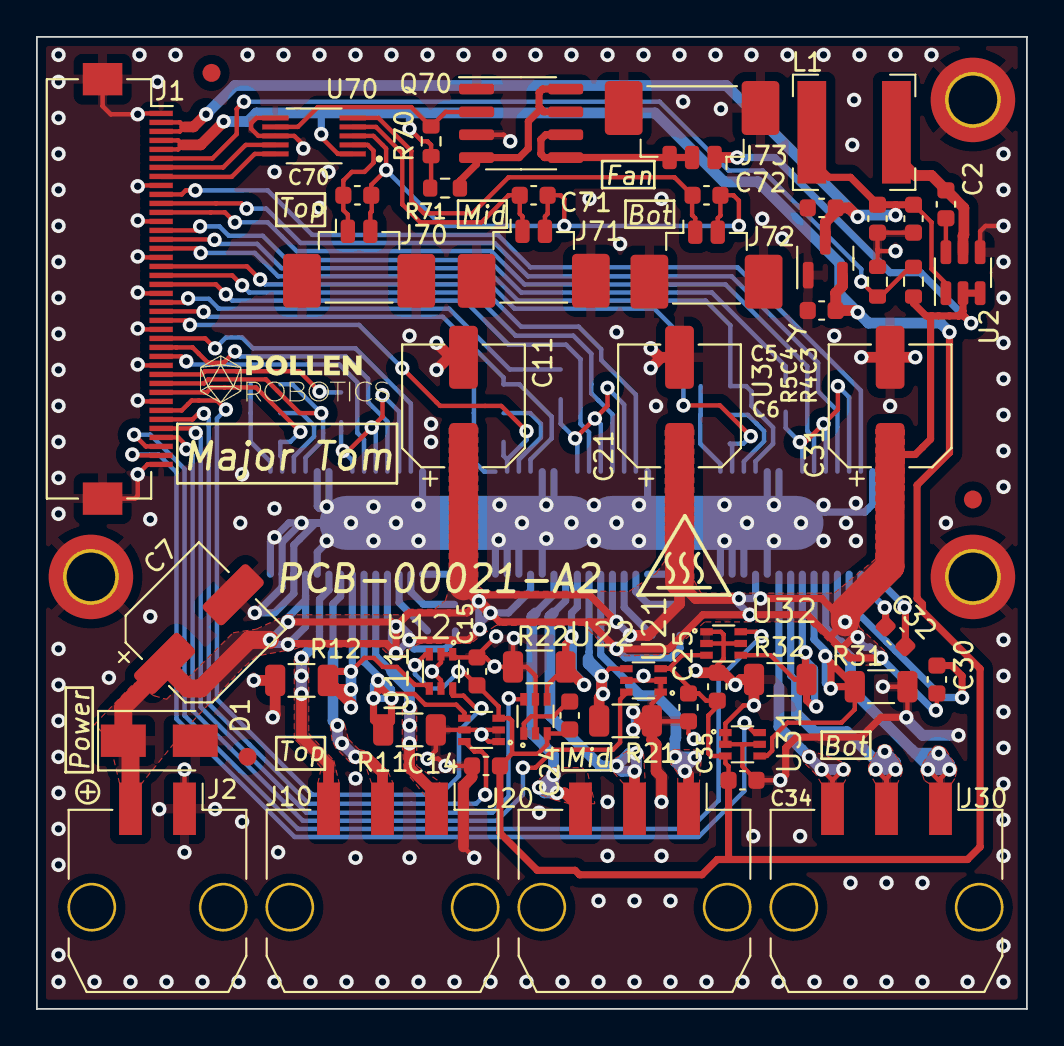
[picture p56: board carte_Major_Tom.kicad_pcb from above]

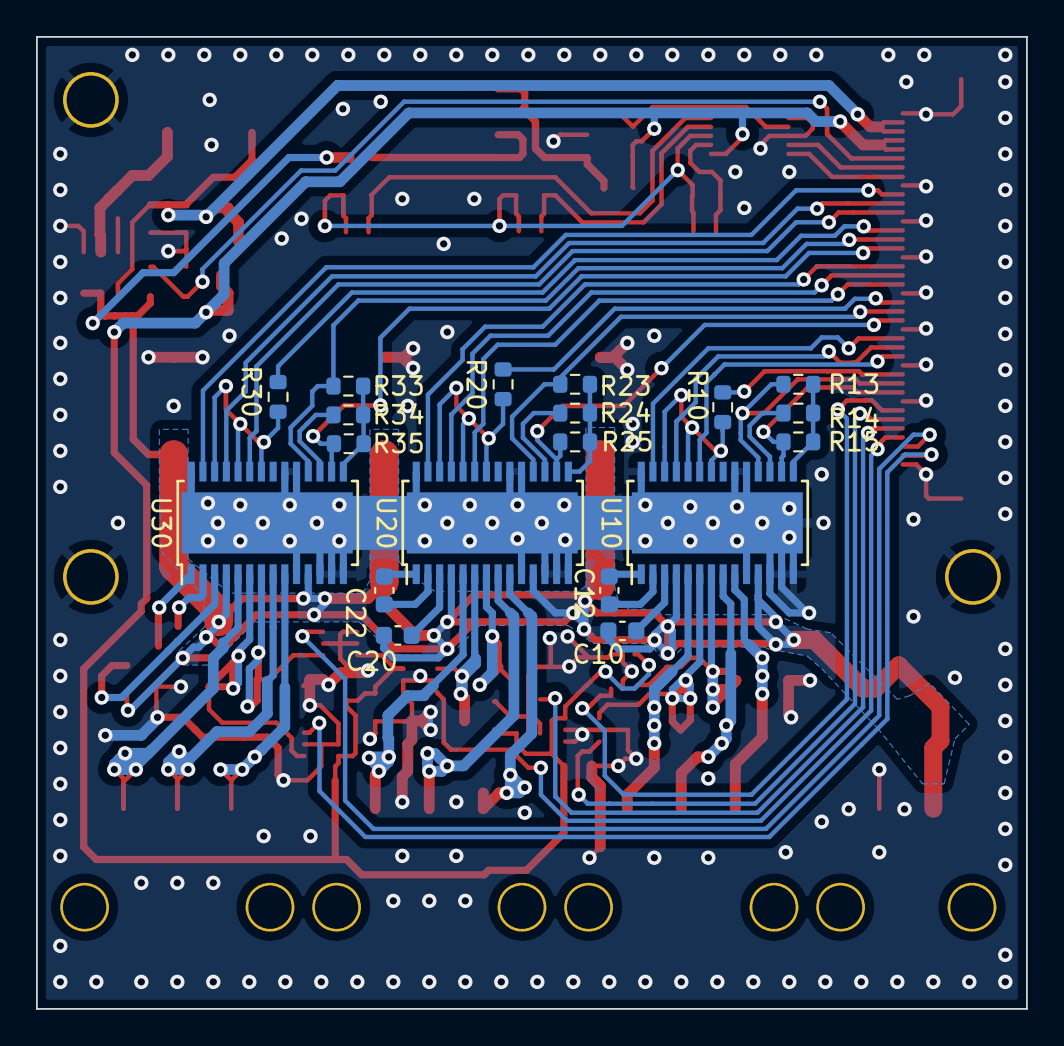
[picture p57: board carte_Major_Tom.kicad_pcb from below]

Board: 2 copper layers, 55.0 x 54.0 mm, 78 parts (19 on the bottom side), 73 nets.

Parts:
C2, C10, C14, C15, C20, C24, C25, C30, C34, C35: 100n 63V; C_0603_1608Metric
C3, C4: 22u 6V3; C_0603_1608Metric
C5, C6: 1u 6V3; C_0603_1608Metric
C7, C11, C21, C31: 10u 63V; CP_Elec_6.3x7.7
C12, C22, C32: 10n 63V; C_0603_1608Metric
C70, C71, C72: 100p; C_0603_1608Metric
D: D_TVS_uni; D_SMA
FID1, FID2, FID3: DNP Fiducial; Fiducial_1mm_Mask2mm
H1, H2, H3: DNP MountingHole_Pad; MountingHole_2.7mm_M2.5_DIN965_Pad_TopOnly
H6: DNP Logo Pollen 2021; Logo_Pollen_2021_sq
J1: FFC 0,5 mm 40w; Hirose_FH12-40S-0.5SH_1x40-1MP_P0.50mm_Horizontal
J2: MicroFit2; Molex_Micro-Fit_3.0_43650-0210_1x02-1MP_P3.00mm_Horizontal
J10, J20, J30: MicroFit3; Molex_Micro-Fit_3.0_43650-0310_1x03-1MP_P3.00mm_Horizontal
J70, J71, J72: Pico2; Molex_PicoBlade_53398-0271_1x02-1MP_P1.25mm_Vertical
J73: Pico3; Molex_PicoBlade_53398-0371_1x03-1MP_P1.25mm_Vertical
L1: 6,8u 2A; L_Bourns-SRN6028
Q70: AUIRF7341Q; SOIC-8_3.9x4.9mm_P1.27mm
R4: 180k; R_0603_1608Metric
R5: 20k; R_0603_1608Metric
R10, R13, R14, R15, R20, R23, R24, R25, R30, R33, R34, R35: 10k; R_0603_1608Metric
R11, R12, R21, R22, R31, R32: 10m; R_1206_3216Metric
R70, R71: 100k; R_0603_1608Metric
SYM1: SYM_Hot_Small; logo_hot
U2: AP63205; TSOT-23-6
U3: MCP1700T; SOT-23
U10, U20, U30: DRV8313; HTSSOP-28-1EP_4.4x9.7mm_P0.65mm_EP3.4x9.5mm
U11, U12, U21, U22, U31, U32: NCS214; SC70-6
U70: MAX31730; SOP50P490X110-10N

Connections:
+3V3: C6.2, C14.2, C15.2, C24.2, C25.2, C34.2, C35.2, J1.4, J1.5, R70.2, R71.2, U3.2 (VO), U11.3 (Vs), U12.3 (Vs), U21.3 (Vs), U22.3 (Vs), U31.3 (Vs), U32.3 (Vs), U70.1 (VDD)
+5V: C3.1, C4.1, C5.1, J1.2, J1.3, L1.1, U2.1 (FB), U3.3 (VI)
+BATT: C7.1, C10.1, C11.1, C20.1, C21.1, C30.1, C31.1, D.1 (A1), J2.2, J73.1, R4.2, U2.2 (EN), U2.3 (IN), U10.4 (VM), U10.11 (VM), U20.4 (VM), U20.11 (VM), U30.4 (VM), U30.11 (VM)
/Fan control/SCL: J1.8, U70.10 (SCL)
/Fan control/SDA: J1.7, U70.9 (SDA)
/Microcontroller/MBotCurrent_A: J1.39, U31.6 (OUT)
/Microcontroller/MBotCurrent_B: J1.38, U32.6 (OUT)
/Microcontroller/MBotPWM_A: J1.10, U30.27 (In1)
/Microcontroller/MBotPWM_B: J1.11, U30.25 (In2)
/Microcontroller/MBotPWM_C: J1.12, U30.23 (In3)
/Microcontroller/MBot_En: J1.14, R30.1
/Microcontroller/MBot_nFault: J1.15, R33.1, U30.18 (nFault)
/Microcontroller/MBot_nRST: J1.16, R35.2, U30.16 (nReset)
/Microcontroller/MMidCurrent_A: J1.37, U21.6 (OUT)
/Microcontroller/MMidCurrent_B: J1.36, U22.6 (OUT)
/Microcontroller/MMidPWM_A: J1.18, U20.27 (In1)
/Microcontroller/MMidPWM_B: J1.19, U20.25 (In2)
/Microcontroller/MMidPWM_C: J1.20, U20.23 (In3)
/Microcontroller/MMid_En: J1.22, R20.1
/Microcontroller/MMid_nFault: J1.23, R23.1, U20.18 (nFault)
/Microcontroller/MMid_nRST: J1.24, R25.2, U20.16 (nReset)
/Microcontroller/MTopCurrent_A: J1.35, U11.6 (OUT)
/Microcontroller/MTopCurrent_B: J1.34, U12.6 (OUT)
/Microcontroller/MTopPWM_A: J1.26, U10.27 (In1)
/Microcontroller/MTopPWM_B: J1.27, U10.25 (In2)
/Microcontroller/MTopPWM_C: J1.28, U10.23 (In3)
/Microcontroller/MTop_En: J1.30, R10.1
/Microcontroller/MTop_nFault: J1.31, R13.1, U10.18 (nFault)
/Microcontroller/MTop_nRST: J1.32, R15.2, U10.16 (nReset)
/Microcontroller/Vbatt_div_10: J1.6, R4.1, R5.2
/Motors/3V3_Drv1: R13.2, R14.1, R15.1, U10.15 (V3P3)
/Motors/3V3_Drv2: R23.2, R24.1, R25.1, U20.15 (V3P3)
/Motors/3V3_Drv3: R33.2, R34.1, R35.1, U30.15 (V3P3)
/Motors/MBotPh1: J30.1, U30.5 (Out1)
/Motors/MBotPh2: J30.2, U30.8 (Out2)
/Motors/MBotPh3: J30.3, U30.9 (Out3)
/Motors/MMidPh1: J20.1, U20.5 (Out1)
/Motors/MMidPh2: J20.2, U20.8 (Out2)
/Motors/MMidPh3: J20.3, U20.9 (Out3)
/Motors/MTopPh1: J10.1, U10.5 (Out1)
/Motors/MTopPh2: J10.2, U10.8 (Out2)
/Motors/MTopPh3: J10.3, U10.9 (Out3)
GND: C3.2, C4.2, C5.2, C6.1, C7.2, C11.2, C14.1, C15.1, C21.2, C24.1, C25.1, C31.2, C34.1, C35.1, D.2 (A2), H1.1, H2.1, H3.1, J1.1, J1.9, J1.13, J1.17, J1.21, J1.25, J1.29, J1.33, J1.40, J1.MP (MountPin), J2.1, J70.MP (MountPin), J71.MP (MountPin), J72.MP (MountPin), J73.MP (MountPin), Q70.1 (S1), Q70.3 (S2), R5.1, R11.2, R12.2, R21.2, R22.2, R31.2, R32.2, U2.4 (GND), U3.1 (GND), U10.10 (PGnd3), U10.12 (CompP), U10.13 (CompN), U10.14 (Gnd), U10.19 (nCompo), U10.20 (Gnd), U10.28 (Gnd), U10.29 (Thermal_Pad), U11.1 (REF), U11.2 (GND), U11.5 (-IN), U12.1 (REF), U12.2 (GND), U12.5 (-IN), U20.10 (PGnd3), U20.12 (CompP), U20.13 (CompN), U20.14 (Gnd), U20.19 (nCompo), U20.20 (Gnd), U20.28 (Gnd), U20.29 (Thermal_Pad), U21.1 (REF), U21.2 (GND), U21.5 (-IN), U22.1 (REF), U22.2 (GND), U22.5 (-IN), U30.10 (PGnd3), U30.12 (CompP), U30.13 (CompN), U30.14 (Gnd), U30.19 (nCompo), U30.20 (Gnd), U30.28 (Gnd), U30.29 (Thermal_Pad), U31.1 (REF), U31.2 (GND), U31.5 (-IN), U32.1 (REF), U32.2 (GND), U32.5 (-IN), U70.6 (GND), U70.8 (ADD)
unnamed: C2.1, U2.6 (BST)
unnamed: C2.2, L1.2, U2.5 (SW)
unnamed: C10.2, U10.3 (VCP)
unnamed: C12.1, U10.1 (CPL)
unnamed: C12.2, U10.2 (CPH)
unnamed: C20.2, U20.3 (VCP)
unnamed: C22.1, U20.1 (CPL)
unnamed: C22.2, U20.2 (CPH)
unnamed: C30.2, U30.3 (VCP)
unnamed: C32.1, U30.1 (CPL)
unnamed: C32.2, U30.2 (CPH)
unnamed: C70.1, C71.1, C72.1, J70.2, J71.2, J72.2, U70.3 (DXN)
unnamed: C70.2, J70.1, U70.2 (DXP1)
unnamed: C71.2, J71.1, U70.4 (DXP2)
unnamed: C72.2, J72.1, U70.5 (DXP3)
unnamed: J73.2, J73.3, Q70.5 (D2), Q70.6 (D2)
unnamed: Q70.2 (G1), R70.1, U70.7 (~THERM)
unnamed: Q70.4 (G2), Q70.7 (D1), Q70.8 (D1), R71.1
unnamed: R10.2, U10.22 (En3), U10.24 (En2), U10.26 (En1)
unnamed: R11.1, U10.6 (PGnd1), U11.4 (+IN)
unnamed: R12.1, U10.7 (PGnd2), U12.4 (+IN)
unnamed: R14.2, U10.17 (nSleep)
unnamed: R20.2, U20.22 (En3), U20.24 (En2), U20.26 (En1)
unnamed: R21.1, U20.6 (PGnd1), U21.4 (+IN)
unnamed: R22.1, U20.7 (PGnd2), U22.4 (+IN)
unnamed: R24.2, U20.17 (nSleep)
unnamed: R30.2, U30.22 (En3), U30.24 (En2), U30.26 (En1)
unnamed: R31.1, U30.6 (PGnd1), U31.4 (+IN)
unnamed: R32.1, U30.7 (PGnd2), U32.4 (+IN)
unnamed: R34.2, U30.17 (nSleep)

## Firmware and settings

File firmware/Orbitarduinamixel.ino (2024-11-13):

// Select board "Generic STM32G4 series"
// and board part number "Generic G474VBTx"

#include <Arduino.h>
#include <SimpleFOC.h>
#include <SimpleFOCDrivers.h>
#include "encoders/as5047/MagneticSensorAS5047.h"
#include <BMI088.h>
#include <Dynamixel2Arduino.h>
#include <IWatchdog.h>

// Firmware Revision (odd = dev, even = stable)
#define ORBITARDUINAMIXEL_REV  1 // Dev for first release

uint8_t orbita_firmware_rev = ORBITARDUINAMIXEL_REV;


#define GREEN_LED  PE0
#define RED_LED    PC13
#define TEST_PIN_2 PB12 // Now used as Bot_Motor_Phase_B
#define TEST_PIN_3 PB13 // Now used as Bot_Motor_Phase_C
#define TEST_PIN_4 PA7

#define WATCHDOG_DELAY 4000000 // us

//      Top

const byte topCSA     = PA0;
const byte topCSB     = PA1;
const byte topEncA    = PA8;
const byte topEncB    = PA9;
const byte topEncI    = PE7;
const byte topHallA   = PA8;
const byte topHallB   = PA9;
const byte topHallC   = PA10;
const byte topMotA    = PD12;
const byte topMotB    = PD13;
const byte topMotC    = PD14;
const byte topMotEn   = PD9;
const byte topMotnRST = PD10;
const byte topMotnFlt = PD11;
#define TOP_MOTOR_CMD 'T'

//      Middle
const byte midCSA     = PB1;
const byte midCSB     = PE9;
const byte midEncA    = PA15;
const byte midEncB    = PD4;
const byte midEncI    = PD3;
const byte midHallA   = PA15;
const byte midHallB   = PD4;
const byte midHallC   = PD7;
const byte midMotA    = PB2;
const byte midMotB    = PC12;
const byte midMotC    = PE8;
const byte midMotEn   = PC1;
const byte midMotnRST = PC2;
const byte midMotnFlt = PC3;
#define MID_MOTOR_CMD 'M'

//      Bottom
const byte botCSA     = PE14;
const byte botCSB     = PE15;
const byte botEncA    = PE2;
const byte botEncB    = PE3;
const byte botEncI    = PD2;
const byte botHallA   = PE2;
const byte botHallB   = PE6; // PE3 on Houston-A1 base
const byte botHallC   = PC0; // PE4 on Houston-A1 base
const byte botMotA    = PC6;
const byte botMotB    = PC7;
const byte botMotC    = PC8;
const byte botMotEn   = PE10;
const byte botMotnRST = PE11;
const byte botMotnFlt = PE12;
#define BOT_MOTOR_CMD 'B'


//      Orbita Magnetic Sensor
const byte orbitaSPI_MOSI  = PB5;
const byte orbitaSPI_MISO  = PB4;
const byte orbitaSPI_SCK   = PA5;
const byte orbitaTopSPI_CS = PA4;
const byte orbitaMidSPI_CS = PB7;
const byte orbitaBotSPI_CS = PB6;
#define ORBITA_SENSOR_TYPE AS5047_SPI

//      Orbita IMU
const byte orbitaIMU_Acc_CS = PA3;
const byte orbitaIMU_Gyr_CS = PB9;

/************************ Motors ***********************/
// Maxon ECX Torque 22 M
#define MOTOR_POLE_PAIRS                4
#define MOTOR_PHASE_RESISTANCE          0.763
#define MOTOR_SPEED_COEFF             645.0
// Maxon ENX 22 (encoder)
#define MOTOR_ENCODER_NB_STEPS        512

#define MOTOR_POWER_SUPPLY             12.0 // Volts
#define MOTOR_VOLTAGE_LIMIT             4.0 // Volts - finaly defines Torque resistance
//#define MOTOR_INTENSITY_LIMIT         100.0 // [Amps] - if phase resistance defined
#define MOTOR_VOLTAGE_SENSOR_ALIGN      1.0 // Volts
#define MOTOR_VELOCITY_PID_P            0.03
#define MOTOR_VELOCITY_PID_I            0.50
#define MOTOR_VELOCITY_PID_D            0.00
#define MOTOR_VELOCITY_OUT_RAMP      1000.0
#define MOTOR_VELOCITY_LPF              0.020 // seconds
#define MOTOR_TORQUE_CONTROLLER TorqueControlType::voltage
#define MOTOR_MOTION_CONTROLLER MotionControlType::velocity

#define DRIVER_RESET_DELAY             10 // ms (should be less than 1 ms)

#define TOP_MOTOR_ZERO_ELEC_ANGLE       3.14
#define TOP_MOTOR_NATURAL_DIRECTION     Direction::CCW
#define MID_MOTOR_ZERO_ELEC_ANGLE       3.14
#define MID_MOTOR_NATURAL_DIRECTION     Direction::CCW
#define BOT_MOTOR_ZERO_ELEC_ANGLE       3.14
#define BOT_MOTOR_NATURAL_DIRECTION     Direction::CW

unsigned int motors_init_started = 0;
unsigned int motors_initialized = 0;

#define HELLO_DURATION_MS            1000
#define HELLO_SIN_FREQ                  2.0
#define HELLO_SIN_AMP                   (PI/2.0)

/********************** Motor Top **********************/
HallSensor top_sensor = HallSensor(topHallA, topHallB, topHallC, MOTOR_POLE_PAIRS);
BLDCDriver3PWM top_driver = BLDCDriver3PWM(topMotA, topMotB, topMotC, topMotEn);
BLDCMotor top_motor = BLDCMotor(MOTOR_POLE_PAIRS);//, MOTOR_PHASE_RESISTANCE, MOTOR_SPEED_COEFF);
void top_DoA() {top_sensor.handleA();}
void top_DoB() {top_sensor.handleB();}
void top_DoC() {top_sensor.handleC();}

/********************** Motor Middle *******************/
HallSensor mid_sensor = HallSensor(midHallA, midHallB, midHallC, MOTOR_POLE_PAIRS);
BLDCDriver3PWM mid_driver = BLDCDriver3PWM(midMotA, midMotB, midMotC, midMotEn);
BLDCMotor mid_motor = BLDCMotor(MOTOR_POLE_PAIRS);//, MOTOR_PHASE_RESISTANCE, MOTOR_SPEED_COEFF);
void mid_DoA() {mid_sensor.handleA();}
void mid_DoB() {mid_sensor.handleB();}
void mid_DoC() {mid_sensor.handleC();}

/********************** Motor Bottom *******************/
HallSensor bot_sensor = HallSensor(botHallA, botHallB, botHallC, MOTOR_POLE_PAIRS);
BLDCDriver3PWM bot_driver = BLDCDriver3PWM(botMotA, botMotB, botMotC, botMotEn);
BLDCMotor bot_motor = BLDCMotor(MOTOR_POLE_PAIRS);//, MOTOR_PHASE_RESISTANCE, MOTOR_SPEED_COEFF);
void bot_DoA() {bot_sensor.handleA();}
void bot_DoB() {bot_sensor.handleB();}
void bot_DoC() {bot_sensor.handleC();}

/********************** Orbita Sensor ******************/

SPIClass SPI_1(orbitaSPI_MOSI, orbitaSPI_MISO, orbitaSPI_SCK);
MagneticSensorAS5047 orbita_top_sensor(orbitaTopSPI_CS);
MagneticSensorAS5047 orbita_mid_sensor(orbitaMidSPI_CS);
MagneticSensorAS5047 orbita_bot_sensor(orbitaBotSPI_CS);
float orbita_top_sensor_target    = 0.0;
float orbita_mid_sensor_target    = 0.0;
float orbita_bot_sensor_target    = 0.0;
float orbita_top_present_position = 0.0;
float orbita_mid_present_position = 0.0;
float orbita_bot_present_position = 0.0;

uint8_t orbita_system_check          = 0x00;
uint8_t orbita_motors_drivers_states = 0x00;
float   orbita_motors_voltage_limit  = MOTOR_VOLTAGE_LIMIT;
uint8_t orbita_torque_enable         = 0x00; // Start with torque disabled

/********************* Orbita PID **********************/
float get_Orbita_PID_control(float target, float current);
// PID Tuning, ultimate Ku is reached at ~6000, oscillations Tu are at 1040 ms
#define ORBITA_PID_DEF_P        500.0f
#define ORBITA_PID_DEF_I          0.000f
#define ORBITA_PID_DEF_D          0.000f
#define ORBITA_PID_DEF_LIMIT    380.0f // Velocity limit
#define ORBITA_PID_DEF_RAMP   10000.0f // Not used

PIDController Orbita_Top_PID {ORBITA_PID_DEF_P, ORBITA_PID_DEF_I, ORBITA_PID_DEF_D, ORBITA_PID_DEF_RAMP, ORBITA_PID_DEF_LIMIT};
PIDController Orbita_Mid_PID {ORBITA_PID_DEF_P, ORBITA_PID_DEF_I, ORBITA_PID_DEF_D, ORBITA_PID_DEF_RAMP, ORBITA_PID_DEF_LIMIT};
PIDController Orbita_Bot_PID {ORBITA_PID_DEF_P, ORBITA_PID_DEF_I, ORBITA_PID_DEF_D, ORBITA_PID_DEF_RAMP, ORBITA_PID_DEF_LIMIT};
#define ORBITA_SENSOR_FILTERING 10 // Taking 1 sensor value out of x foc_loop()

/*********************** BMI088 ************************/
Bmi088Accel accel(SPI_1, orbitaIMU_Acc_CS);
Bmi088Gyro  gyro (SPI_1, orbitaIMU_Gyr_CS);

/******************** Dynamixelisation *****************/
#define DXL_SERIAL       Serial3
#define DEBUG_SERIAL     Serial
#define DXL_BAUDRATE      1000000
#define DXL_FIRM_VERSION  1
#define DXL_DEFAULT_ID   70

const int DXL_DIR_PIN = -1;
const float DXL_PROTOCOL_VER_1_0 = 1.0;
const uint16_t DXL_MODEL_NUM = 0x5005;

DYNAMIXEL::SerialPortHandler dxl_port(DXL_SERIAL, DXL_DIR_PIN);
DYNAMIXEL::Slave dxl(dxl_port, DXL_MODEL_NUM);

const uint16_t DXL_REG_ADDR_MODEL_NUMBER            =  0; // DXL_MODEL_NUM
const uint16_t DXL_REG_ADDR_FIRMWARE_REV            =  6; // orbita_firmware_rev
const uint16_t DXL_REG_ADDR_ID                      =  7; // DXL_DEFAULT_ID
const uint16_t DXL_REG_ADDR_SYSTEM_CHECK            =  8; // orbita_system_check
#define DXL_REG_MASK_SYS_RESET       0x80
#define DXL_REG_MASK_BLINK_10S       0x01
const uint16_t DXL_REG_ADDR_MOTORS_DRIVERS_STATES   =  9; // orbita_motors_drivers_states
#define DXL_REG_BIT_TOP_MOTOR_STATE  7
#define DXL_REG_BIT_MID_MOTOR_STATE  6
#define DXL_REG_BIT_BOT_MOTOR_STATE  5
#define DXL_REG_BIT_TOP_DRIVER_STATE 4
#define DXL_REG_BIT_MID_DRIVER_STATE 3
#define DXL_REG_BIT_BOT_DRIVER_STATE 2
const uint16_t DXL_REG_ADDR_MOTOR_VOLTAGE_LIMIT     = 10; // top_motor.voltage_limit

const uint16_t DXL_REG_ADDR_MOTOR_VEL_PID_P         = 18; // top_motor.PID_velocity.P
const uint16_t DXL_REG_ADDR_MOTOR_VEL_PID_I         = 22; // top_motor.PID_velocity.I
const uint16_t DXL_REG_ADDR_MOTOR_VEL_PID_D         = 26; // top_motor.PID_velocity.D
const uint16_t DXL_REG_ADDR_MOTOR_VEL_RAMP_OUT      = 30; // top_motor.PID_velocity.output_ramp
const uint16_t DXL_REG_ADDR_MOTOR_VEL_LP_FILTER     = 34; // top_motor.LPF_velocity.Tf
const uint16_t DXL_REG_ADDR_ORBITA_PID_P            = 38; // Orbita_Top_PID.P
const uint16_t DXL_REG_ADDR_ORBITA_PID_I            = 42; // Orbita_Top_PID.I
const uint16_t DXL_REG_ADDR_ORBITA_PID_D            = 46; // Orbita_Top_PID.D
const uint16_t DXL_REG_ADDR_ORBITA_VEL_LIMIT        = 50; // Orbita_Top_PID.limit

const uint16_t DXL_REG_ADDR_TORQUE_ENABLE           = 58; // orbita_torque_enable
const uint16_t DXL_REG_ADDR_TOP_GOAL_POSITION       = 59; // orbita_top_sensor_target
const uint16_t DXL_REG_ADDR_MID_GOAL_POSITION       = 63; //   ''   mid   ''     ''
const uint16_t DXL_REG_ADDR_BOT_GOAL_POSITION       = 67; //   ''   bot   ''     ''
const uint16_t DXL_REG_ADDR_TOP_PRESENT_POSITION    = 71; // orbita_top_present_position
const uint16_t DXL_REG_ADDR_MID_PRESENT_POSITION    = 75; //   ''   mid   ''     ''
const uint16_t DXL_REG_ADDR_BOT_PRESENT_POSITION    = 79; //   ''   bot   ''     ''

/*******************************************************/

HardwareSerial Serial3(PB11, PB10);  // Houston-J7

void top_init();
void mid_init();
void bot_init();
void top_loop();
void mid_loop();
void bot_loop();

void init_Pacman();

void hello_motors(unsigned int);
void red_alert();
void zen_again();

void init_IO() {
  // Top
  pinMode(topEncA,  INPUT_FLOATING);
  pinMode(topEncB,  INPUT_FLOATING);
  pinMode(topEncI,  INPUT_FLOATING);
  pinMode(topHallA, INPUT_FLOATING);
  pinMode(topHallB, INPUT_FLOATING);
  pinMode(topHallC, INPUT_FLOATING);
  pinMode(topMotA,  OUTPUT_PP);
  pinMode(topMotB,  OUTPUT_PP);
  pinMode(topMotC,  OUTPUT_PP);
  pinMode(topMotEn, OUTPUT_PP);
  pinMode(topMotnRST, INPUT_FLOATING);
  pinMode(topMotnFlt, INPUT_FLOATING);
  pinMode(topCSA,   INPUT_ANALOG);
  pinMode(topCSB,   INPUT_ANALOG);

  digitalWrite(topMotA,  LOW);
  digitalWrite(topMotB,  LOW);
  digitalWrite(topMotC,  LOW);
  digitalWrite(topMotEn, LOW);

  // Middle
  pinMode(midEncA,  INPUT_FLOATING);
  pinMode(midEncB,  INPUT_FLOATING);
  pinMode(midEncI,  INPUT_FLOATING);
  pinMode(midHallA, INPUT_FLOATING);
  pinMode(midHallB, INPUT_FLOATING);
  pinMode(midHallC, INPUT_FLOATING);
  pinMode(midMotA,  OUTPUT_PP);
  pinMode(midMotB,  OUTPUT_PP);
  pinMode(midMotC,  OUTPUT_PP);
  pinMode(midMotEn, OUTPUT_PP);
  pinMode(midMotnRST, INPUT_FLOATING);
  pinMode(midMotnFlt, INPUT_FLOATING);
  pinMode(midCSA,   INPUT_ANALOG);
  pinMode(midCSB,   INPUT_ANALOG);

  digitalWrite(midMotA,  LOW);
  digitalWrite(midMotB,  LOW);
  digitalWrite(midMotC,  LOW);
  digitalWrite(midMotEn, LOW);

  // Bottom
  pinMode(botEncA,  INPUT_FLOATING);
  pinMode(botEncB,  INPUT_FLOATING);
  pinMode(botEncI,  INPUT_FLOATING);
  pinMode(botHallA, INPUT_FLOATING);
  pinMode(botHallB, INPUT_FLOATING);
  pinMode(botHallC, INPUT_FLOATING);
  pinMode(botMotA,  OUTPUT_PP);
  pinMode(botMotB,  OUTPUT_PP);
  pinMode(botMotC,  OUTPUT_PP);
  pinMode(botMotEn, OUTPUT_PP);
  pinMode(botMotnRST, INPUT_FLOATING);
  pinMode(botMotnFlt, INPUT_FLOATING);
  pinMode(botCSA,   INPUT_ANALOG);
  pinMode(botCSB,   INPUT_ANALOG);

  digitalWrite(botMotA,  LOW);
  digitalWrite(botMotB,  LOW);
  digitalWrite(botMotC,  LOW);
  digitalWrite(botMotEn, LOW);
}


void setup_bitbang_hall_testing() {
  pinMode(topHallA, INPUT);
  pinMode(topHallB, INPUT);
  pinMode(topHallC, INPUT);
  pinMode(midHallA, INPUT);
  pinMode(midHallB, INPUT);
  pinMode(midHallC, INPUT);
  pinMode(botHallA, INPUT);
  pinMode(botHallB, INPUT);
  pinMode(botHallC, INPUT);
}
void loop_bitbang_hall_testing() {
    Serial3.print("\tTOP_rd: ");
    Serial3.print(digitalRead(topHallA));
    Serial3.print(digitalRead(topHallB));
    Serial3.print(digitalRead(topHallC));

    Serial3.print("\tMID_bl: ");
    Serial3.print(digitalRead(midHallA));
    Serial3.print(digitalRead(midHallB));
    Serial3.print(digitalRead(midHallC));

    Serial3.print("\tBOT_yl: ");
    Serial3.print(digitalRead(botHallA));
    Serial3.print(digitalRead(botHallB));
    Serial3.print(digitalRead(botHallC));
    Serial3.println();
}


void setup() {
  init_IO();
  //BMI fix
  pinMode(orbitaIMU_Acc_CS, OUTPUT);
  digitalWrite(orbitaIMU_Acc_CS, HIGH);
  pinMode(orbitaIMU_Gyr_CS, OUTPUT);
  digitalWrite(orbitaIMU_Gyr_CS, HIGH);








  pinMode(RED_LED, OUTPUT);
  pinMode(GREEN_LED, OUTPUT);
  pinMode(TEST_PIN_4, OUTPUT);
  digitalWrite(RED_LED, HIGH);
  digitalWrite(GREEN_LED, LOW);
  digitalWrite(TEST_PIN_4, LOW);

  //  delay(1000); // Connecting time
  delay(250);  // Just flashing
  digitalWrite(RED_LED, LOW);

  pinMode(topMotnFlt, INPUT_FLOATING);
  pinMode(midMotnFlt, INPUT_FLOATING);
  pinMode(botMotnFlt, INPUT_FLOATING);
  //attachInterrupt(digitalPinToInterrupt(topMotnFlt), red_alert, FALLING);
  //attachInterrupt(digitalPinToInterrupt(midMotnFlt), red_alert, FALLING);
  //attachInterrupt(digitalPinToInterrupt(botMotnFlt), red_alert, FALLING);
  //attachInterrupt(digitalPinToInterrupt(topMotnFlt), zen_again, RISING);
  //attachInterrupt(digitalPinToInterrupt(midMotnFlt), zen_again, RISING);
  //attachInterrupt(digitalPinToInterrupt(botMotnFlt), zen_again, RISING);

  Serial3.begin(115200);
  SimpleFOCDebug::enable(&Serial3);
  Serial3.print("\r\n\r\n\r\n\r\n\r\n\r\n\r\n\r\n\r\n\r\n\r\n");
  Serial3.println(F("=== Pollen Robotics: Orbita3D ==="));
  Serial3.print(F("CPU_freq: "));
  Serial3.print(F_CPU/1000000);
  Serial3.println(F("MHz"));
  Serial3.print(F("Power supply: "));
  Serial3.println(bot_driver.voltage_power_supply);

Serial3.println("-------------------------------------------top:"); 
  top_init();
    

  Serial3.println("-------------------------------------------mid:"); 
  mid_init();

  Serial3.println("-------------------------------------------bot:"); 
  bot_init();




  Serial3.println("OK");


/*
  setup_bitbang_hall_testing();
  while(true)
  {
    loop_bitbang_hall_testing();
    delay(100);
  } 
*/

  if (motors_initialized != motors_init_started)
    while (true) {
      Serial3.print  (F("Wrong init ("));
      Serial3.print  (motors_initialized);
      Serial3.print  ('/');
      Serial3.print  (motors_init_started);
      Serial3.println(F(" motors initialized)"));
      digitalWrite(RED_LED, !digitalRead(RED_LED));
      delay(10000);
    }
    
  init_Pacman();
//  hello_motors(HELLO_DURATION_MS);
  Serial3.println("--------------------------------done!");

  
  Serial3.end();

  dxl_port.begin(DXL_BAUDRATE);
  dxl.setPortProtocolVersion(DXL_PROTOCOL_VER_1_0);
  dxl.setFirmwareVersion(DXL_FIRM_VERSION);
  dxl.setID(DXL_DEFAULT_ID);
  init_Dynamixel_registers();

  IWatchdog.begin(WATCHDOG_DELAY);
  digitalWrite(GREEN_LED, HIGH);
}

void loop() {
  top_loop(); // from 12 to 26us @10kHz (with 1 PID calculation out of 10 loops)
              //    -> 28% calculation time
              // Motor_Hall_IT: 2,5us. At 4 Volts_max, 7 IT for 7,84 ms
              //    -> 0,2% calculation time
  mid_loop();
  bot_loop();
  Orbita_loop(); // 142 us @1kHz
  if (dxl.processPacket() == false) { // up to 80 us
    red_alert();
  }
  Orbita_update_slow_registers();
  Orbita_polling_faulty_driver();
}

void Orbita_update_slow_registers() {
  // static uint16_t dec = 0;

  // if(dec++ > 10000) { // Every seconds
// digitalWrite(TEST_PIN_4, HIGH);
    // dec = 0;

static bool is_enabled = !orbita_torque_enable;

    if (orbita_torque_enable) {
      if (!is_enabled) {
        zen_again();

        // Target is set to actual position so that Orbita 
        // stays where it is after re-enabling motors.
        orbita_top_sensor.update();
        orbita_mid_sensor.update();
        orbita_bot_sensor.update();
        orbita_top_present_position = orbita_top_sensor.getAngle();
        orbita_mid_present_position = orbita_mid_sensor.getAngle();
        orbita_bot_present_position = orbita_bot_sensor.getAngle();
        orbita_top_sensor_target    = orbita_top_present_position;
        orbita_mid_sensor_target    = orbita_mid_present_position;
        orbita_bot_sensor_target    = orbita_bot_present_position;

        top_motor.enable();
        mid_motor.enable();
        bot_motor.enable();

        is_enabled = true;
      }
    } else {
      if (is_enabled) {
        red_alert();
        top_motor.disable();
        mid_motor.disable();
        bot_motor.disable();

        is_enabled = false;
      }
    }

    if (true) {
      // Propagating top_motor/Orbita parameters to middle and bottom 
      mid_motor.voltage_limit = top_motor.voltage_limit;
      bot_motor.voltage_limit = top_motor.voltage_limit;
      mid_motor.PID_velocity.P = top_motor.PID_velocity.P;
      bot_motor.PID_velocity.P = top_motor.PID_velocity.P;
      mid_motor.PID_velocity.I = top_motor.PID_velocity.I;
      bot_motor.PID_velocity.I = top_motor.PID_velocity.I;
      mid_motor.PID_velocity.D = top_motor.PID_velocity.D;
      bot_motor.PID_velocity.D = top_motor.PID_velocity.D;
      mid_motor.PID_velocity.output_ramp  = top_motor.PID_velocity.output_ramp;
      bot_motor.PID_velocity.output_ramp  = top_motor.PID_velocity.output_ramp;
      mid_motor.LPF_velocity.Tf = top_motor.LPF_velocity.Tf;
      bot_motor.LPF_velocity.Tf = top_motor.LPF_velocity.Tf;

      Orbita_Mid_PID.P = Orbita_Top_PID.P;
      Orbita_Bot_PID.P = Orbita_Top_PID.P;
      Orbita_Mid_PID.I = Orbita_Top_PID.I;
      Orbita_Bot_PID.I = Orbita_Top_PID.I;
      Orbita_Mid_PID.D = Orbita_Top_PID.D;
      Orbita_Bot_PID.D = Orbita_Top_PID.D;
      Orbita_Mid_PID.limit = Orbita_Top_PID.limit;
      Orbita_Bot_PID.limit = Orbita_Top_PID.limit;
    }

    if(orbita_system_check & DXL_REG_MASK_SYS_RESET)
      orbita_reset();
    if(orbita_system_check & DXL_REG_MASK_BLINK_10S)
      blinking_green_and_red_led_for_10_s();
  // }
// digitalWrite(TEST_PIN_4, LOW);
}

void Orbita_polling_faulty_driver() {
  static uint16_t dec = 0;

  if(dec++ > 10000) { // Every seconds
    dec = 0;
    if(!digitalRead(topMotnFlt)) {
      bitSet(orbita_motors_drivers_states, DXL_REG_BIT_TOP_DRIVER_STATE);
//red_alert_blinking(); // block
      red_alert();
    }
    if(!digitalRead(midMotnFlt)) {
      bitSet(orbita_motors_drivers_states, DXL_REG_BIT_MID_DRIVER_STATE);
//red_alert_blinking(); // block
      red_alert();
    }
    if(!digitalRead(botMotnFlt)) {
      bitSet(orbita_motors_drivers_states, DXL_REG_BIT_BOT_DRIVER_STATE);
//red_alert_blinking(); // block
      red_alert();
    }
  }
}

void top_loop() {
  top_motor.loopFOC();  // 17,5us on Nucleo-F401RE @84MHz
  top_motor.move();     // 12us
/*  top_present_position = top_sensor.getAngle();
  if (dxl.processPacket() == false) {
    red_alert();
  }*/
}

void mid_loop() {
  mid_motor.loopFOC();  // 16 us on Houston @150MHz (motor velocity 1000 rad/s)
  mid_motor.move();     //  9 us on Houston @150MHz (motor velocity 1000 rad/s)
/*  mid_present_position = mid_sensor.getAngle();
  if (dxl.processPacket() == false) {
    red_alert();
  }*/
}

void bot_loop() {
  bot_motor.loopFOC();
  bot_motor.move();
/*  bot_present_position = bot_sensor.getAngle();
  if (dxl.processPacket() == false) {
    red_alert();
  }*/
}

void Orbita_loop() {
  // 140us every 1,09 ms (filtering 1/10) -> 13%
  static uint8_t orbita_sensor_filtering_idx = 0;
  if(orbita_sensor_filtering_idx++ > ORBITA_SENSOR_FILTERING) {
    orbita_sensor_filtering_idx = 0;

    IWatchdog.reload();

    // Getting position from Pacman
    orbita_top_sensor.update(); // 46us
    orbita_mid_sensor.update();
    orbita_bot_sensor.update();
    orbita_top_present_position = orbita_top_sensor.getAngle();
    orbita_mid_present_position = orbita_mid_sensor.getAngle();
    orbita_bot_present_position = orbita_bot_sensor.getAngle();

    // Setting commands to motors -> command = pid ( target - measurement )
    // 8 us every 1,07 ms (filtering 1/10)
    top_motor.target = Orbita_Top_PID(orbita_top_sensor_target - orbita_top_present_position);
    top_motor.target *= -1.0;
    mid_motor.target = Orbita_Mid_PID(orbita_mid_sensor_target - orbita_mid_present_position);
    mid_motor.target *= -1.0;
    bot_motor.target = Orbita_Bot_PID(orbita_bot_sensor_target - orbita_bot_present_position);
    bot_motor.target *= -1.0;
  }
}
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

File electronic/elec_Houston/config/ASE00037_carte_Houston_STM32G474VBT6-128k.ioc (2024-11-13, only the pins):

Mcu.UserName=STM32G474VBTx
PA0.Signal=ADC1_IN1
PA1.Signal=ADC1_IN2
PA10.Signal=S_TIM1_CH3
PA11.Signal=USB_DM
PA12.Signal=USB_DP
PA13.Signal=SYS_JTMS-SWDIO
PA14.Signal=SYS_JTCK-SWCLK
PA15.Signal=S_TIM2_CH1
PA3.Signal=GPIO_Output
PA4.Signal=GPIO_Output
PA5.Signal=SPI1_SCK
PA6.Signal=ADC2_IN3
PA7.Signal=ADC2_IN4
PA8.Signal=S_TIM1_CH1
PA9.Signal=S_TIM1_CH2
PB1.Signal=ADC3_IN1
PB10.Signal=USART3_TX
PB11.Signal=USART3_RX
PB12.Signal=GPIO_Output
PB13.Signal=GPIO_Output
PB14.Signal=GPIO_Output
PB2.Signal=S_TIM5_CH1
PB3.Signal=SYS_JTDO-SWO
PB4.Signal=SPI1_MISO
PB5.Signal=SPI1_MOSI
PB6.Signal=GPIO_Output
PB7.Signal=GPIO_Output
PC1.Signal=GPIO_Output
PC12.Signal=S_TIM5_CH2
PC13.Signal=GPIO_Output
PC2.Signal=GPIO_Output
PC3.Signal=GPIO_Input
PC4.Signal=I2C2_SCL
PC6.Signal=S_TIM8_CH1
PC7.Signal=S_TIM8_CH2
PC8.Signal=S_TIM8_CH3
PD10.Signal=GPIO_Output
PD11.Signal=GPIO_Input
PD12.Signal=S_TIM4_CH1
PD13.Signal=S_TIM4_CH2
PD14.Signal=S_TIM4_CH3
PD2.Signal=S_TIM3_ETR
PD3.Signal=S_TIM2_ETR
PD4.Signal=S_TIM2_CH2
PD7.Signal=S_TIM2_CH3
PD9.Signal=GPIO_Output
PE0.Signal=GPIO_Output
PE10.Signal=GPIO_Output
PE11.Signal=GPIO_Output
PE12.Signal=GPIO_Input
PE14.Signal=ADC4_IN1
PE15.Signal=ADC4_IN2
PE2.Signal=S_TIM3_CH1
PE3.Signal=S_TIM3_CH2
PE4.Signal=S_TIM3_CH3
PE7.Signal=S_TIM1_ETR
PE8.Signal=S_TIM5_CH3
PE9.Signal=ADC3_IN2
PF0-OSC_IN.Signal=I2C2_SDA

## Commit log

2024-11-13 [added] Cables/Firmware/Electronic
2024-11-13 [added] Production files for Electronic
    [ASE00036-A1_elec_Pacman_BOM.xlsx, ASE00036-B1_elec_Pacman_BOM.xlsx, ASE00037-A1_carte_Houston_BOM.xlsx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]
2024-11-13 [added] Mechanical parts
    [Iglidur.3mf, MP00001-A1_Basement.step, MP00001-A2_Basement.step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]
2024-11-13 [added] Screeshot of Full assembly
